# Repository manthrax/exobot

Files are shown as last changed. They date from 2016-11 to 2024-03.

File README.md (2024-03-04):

https://manthrax.github.io/exobot/index.html



BOM:

DROK DC Buck Converter x2
https://www.amazon.com/DROK-Numerical-Switching-Adjustable-Stabilizers/dp/B00BYTEHQO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

8*2 = 16$

Adafruit 16-Channel PWM / Servo HAT for Raspberry Pi - Mini Kit

https://www.amazon.com/Adafruit-16-Channel-PWM-Servo-Raspberry/dp/B00SI1SPHS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

20$ bucks.

Raspberry Pi 3 Model B Motherboard
https://www.amazon.com/Raspberry-Pi-RASP-PI-3-Model-Motherboard/dp/B01CD5VC92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
37$

TowerPro SG90 9G Micro Servo 10pk For RC Airplane Boat Helicopter Robot Controls
https://www.amazon.com/TowerPro-Micro-Airplane-Helicopter-Controls/dp/B01D6FEI1W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

22$

16+20+37+22 = 95$

sudo apt-get update
sudo apt-get install node
sudo npm install http
sudo npm install express
sudo npm install ws
sudo npm install adafruit-pca9685

sudo nano /etc/rc.local

Add this before the "exit 0" line.. this makes the bot code launch at startup.

su pi -c '~/bot/exobot/nodebot.sh < /dev/null &'

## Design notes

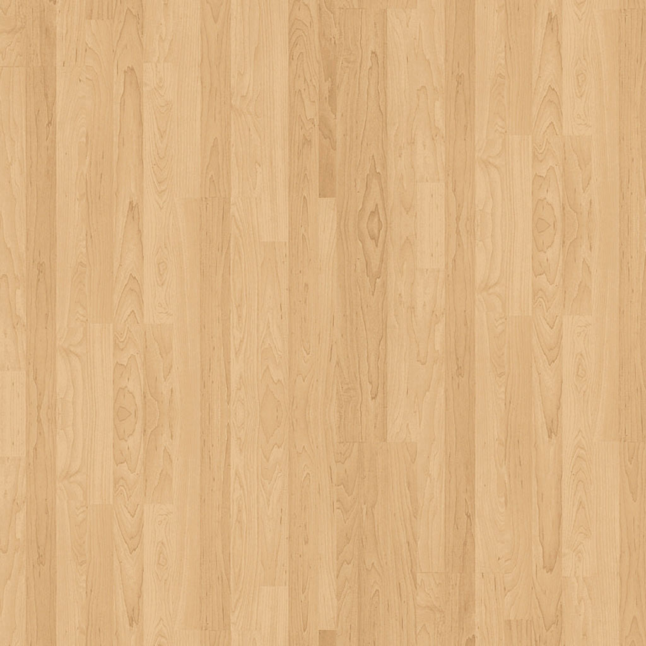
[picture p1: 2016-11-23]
woodfloor.jpg

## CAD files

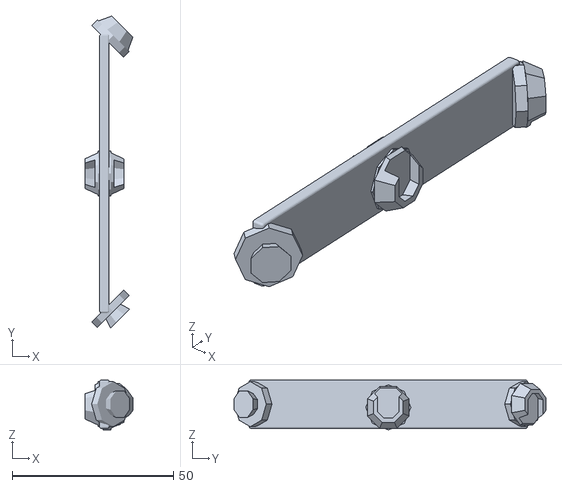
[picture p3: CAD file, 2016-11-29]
design/quadStrut.stl
14.8 x 96.7 x 15.5

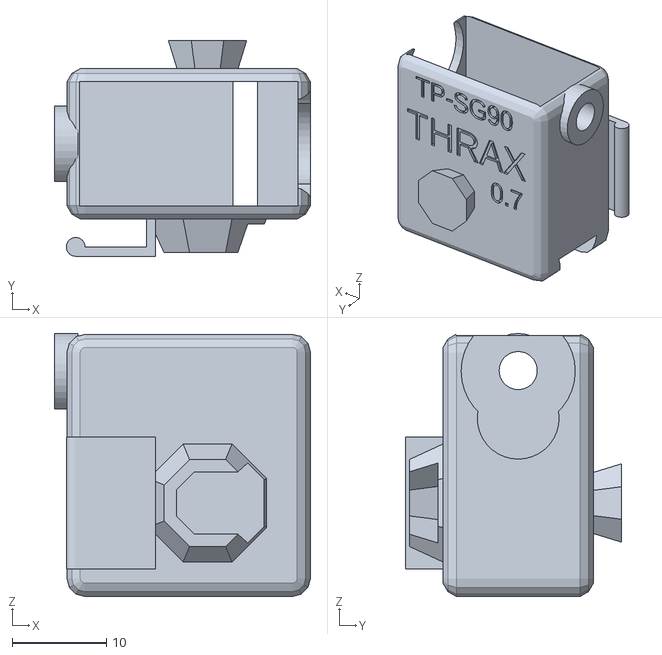
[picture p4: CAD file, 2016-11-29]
design/servoSleeveWithConnectors.stl
27.2 x 22.9 x 27.9

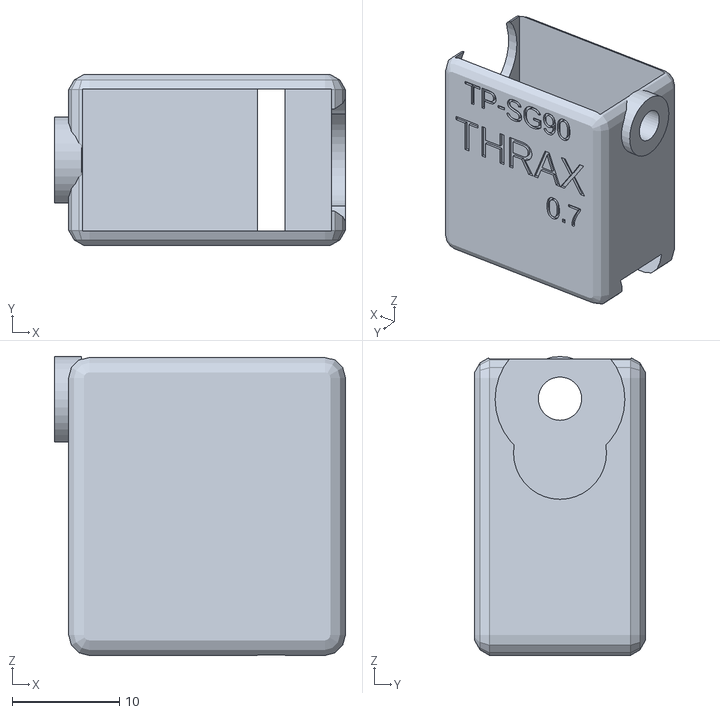
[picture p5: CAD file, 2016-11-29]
design/servoSleeve.stl
27.2 x 16.0 x 27.9

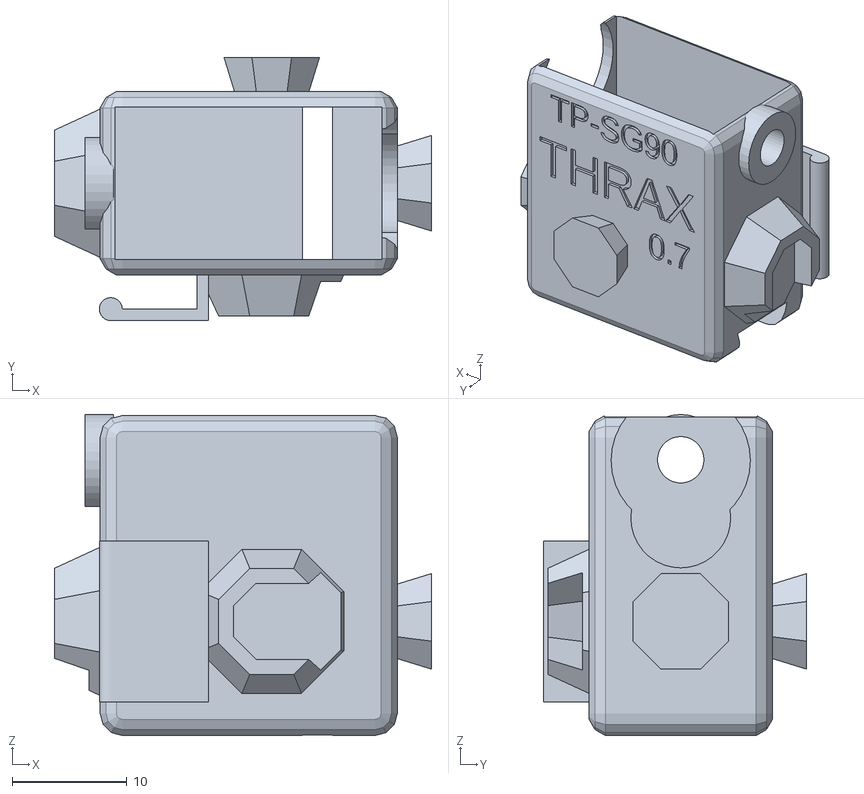
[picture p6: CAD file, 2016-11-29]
design/servoSleeveWithMultiConnectors.stl
32.8 x 22.9 x 27.9

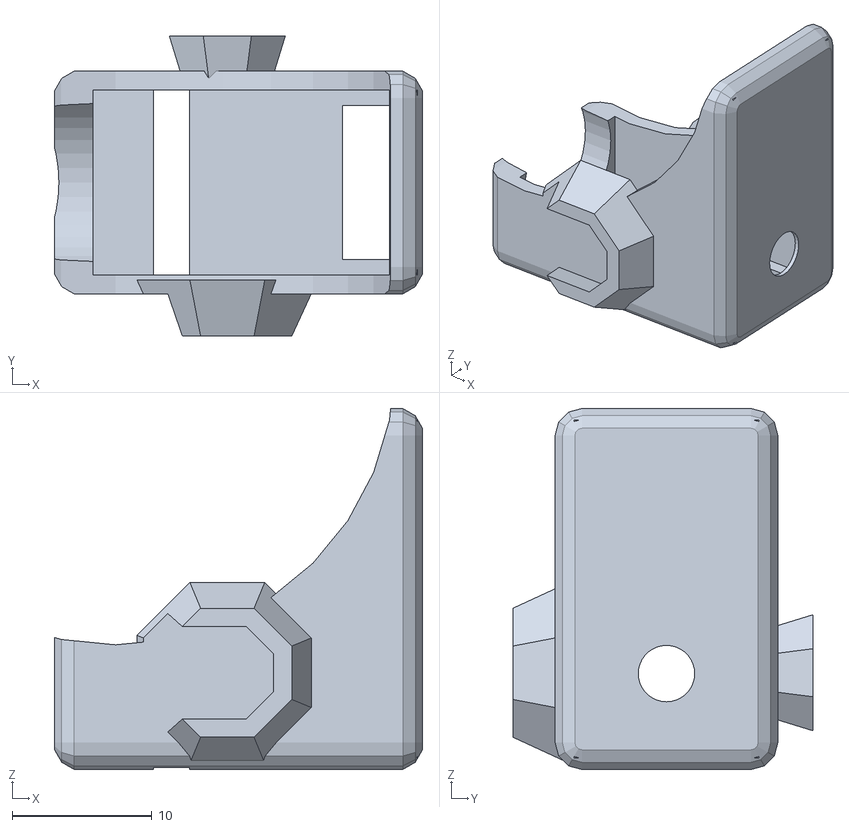
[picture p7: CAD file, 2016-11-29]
design/servoCage.stl
26.4 x 21.5 x 25.9

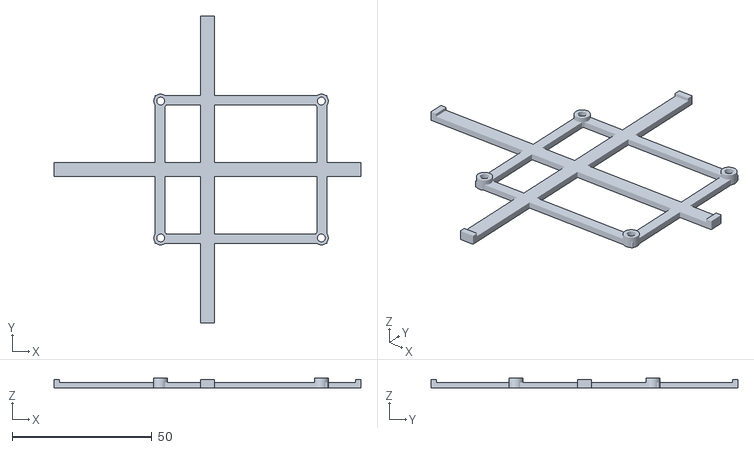
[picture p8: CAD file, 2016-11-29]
design/rackPi.stl
109.9 x 109.9 x 3.55

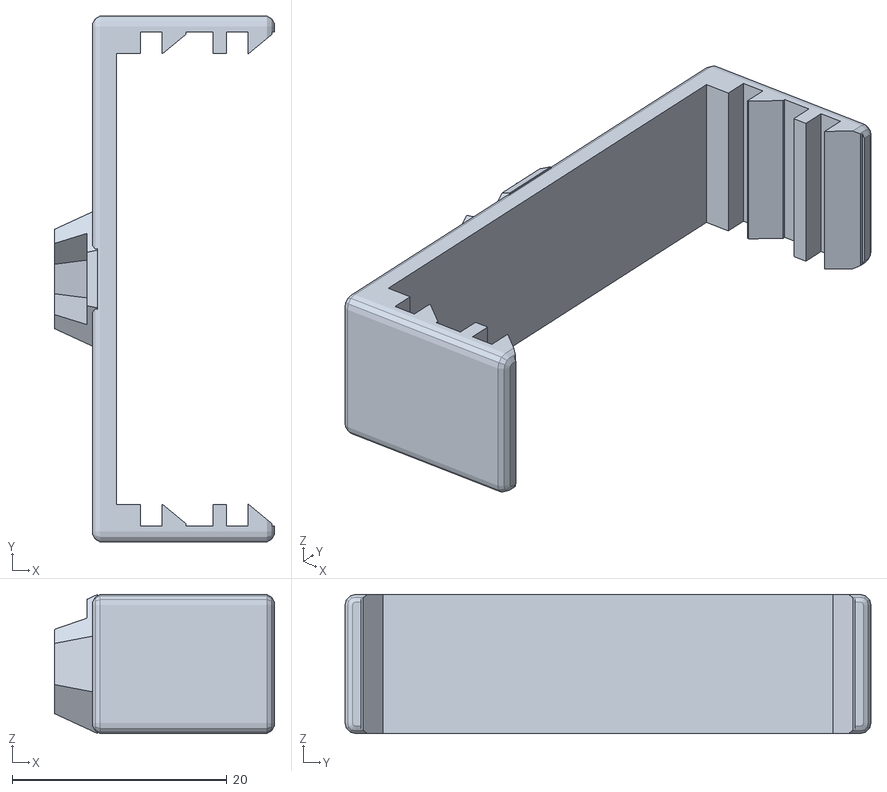
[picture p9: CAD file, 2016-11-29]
design/sensorClamp.stl
20.5 x 48.9 x 12.9

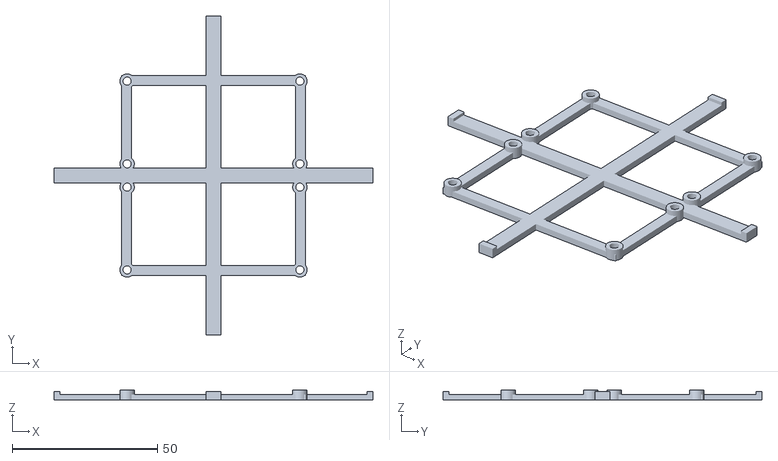
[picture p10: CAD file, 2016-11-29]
design/rackBuck.stl
109.9 x 109.9 x 3.55

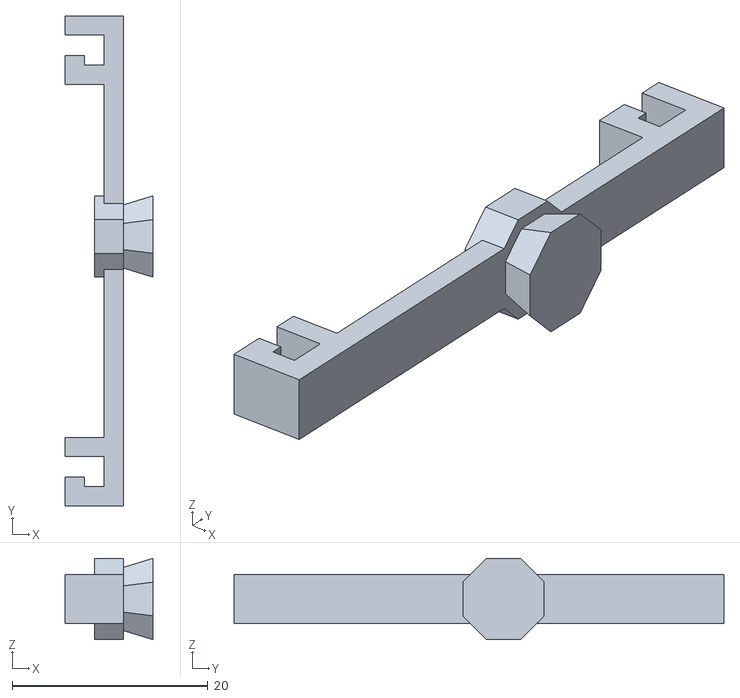
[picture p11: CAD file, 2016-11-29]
design/rackShelfClip.stl
9.00 x 50.0 x 8.31

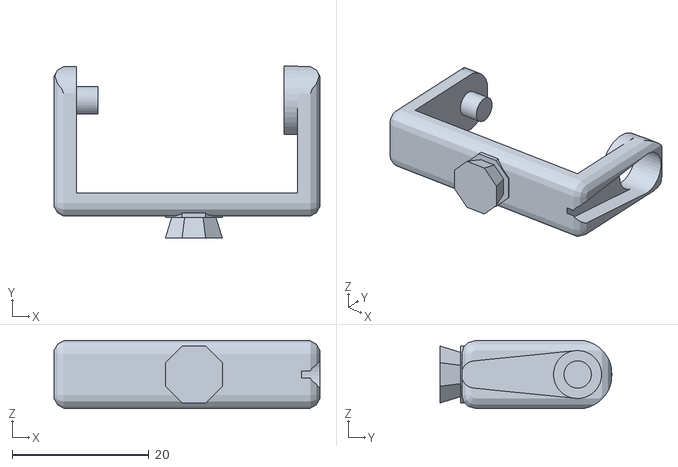
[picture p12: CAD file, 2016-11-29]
design/servoArm.stl
38.9 x 25.1 x 10.00

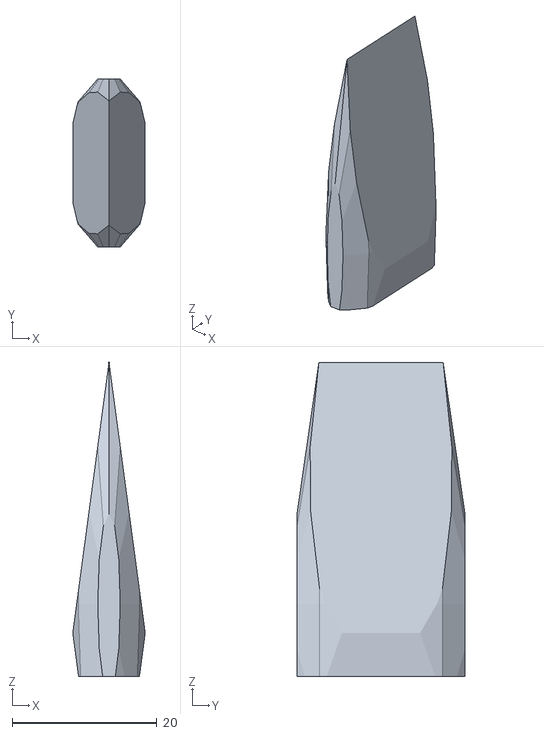
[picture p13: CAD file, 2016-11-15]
design/foot.stl
10.0 x 23.2 x 43.3

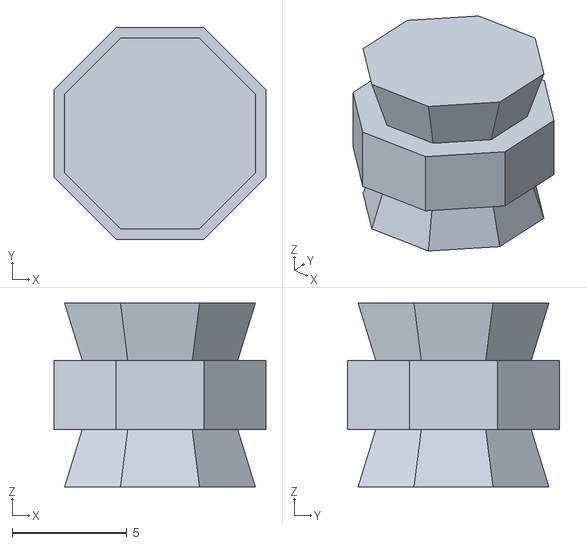
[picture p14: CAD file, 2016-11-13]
design/m2m.stl
9.24 x 9.24 x 8.00

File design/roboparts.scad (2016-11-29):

// CSG-modules.scad - Basic usage of modules, if, color, $fs/$fa

// Change this to false to remove the helper geometry
debug = true;

// Global resolution
$fa = 5;    // Don't generate larger angles than 5 degrees
$fs = 0.2;  // Don't generate smaller facets than 0.1 mm
$fa = 10;    // Don't generate larger angles than 5 degrees

scaleFudge = 1.01;
roundCubes = true;

versionNo = "0.7";

//servoTabLength = 5;

wallThickness = 3;
//Radioshack 2730765
servoName = "RShack";
servoTabLength = 6;
servoBodyWidth = 12;
servoBodyHeight = 21;
servoTabThickness = 2.1;


//TowerPro SG-90
servoName = "TP-SG90";
servoTabLength = 8;//how far the tab sticks out
servoBodyWidth = 13.1;
servoBodyHeight = 23;
servoTabThickness = 2.58;



// Main geometry

//Render the part
partsOnly = true ;
legInset = 32;
nside = 4;  //Number of legs 6 = hexapod
segAngle = 360/nside;

baseRadius = 75;//54;

hardwareZOffset = -1;

piVerticalOffset = 8.5;
battVerticalOffset = -18;
buckVerticalOffset = 36.5;


br = baseRadius;
sa = segAngle;

//pp1 = [sin(0)*br,cos(0)*br,0];
//pp2 = [sin(sa)*br,cos(sa)*br,0];


function rvec(x,y,a) = [(sin(a)*x)+(cos(a)*y),(-cos(a)*x)+(sin(a)*y),0]; 

bo =   14;
pp1 = rvec(br,bo,0);
pp2 = rvec(br,-bo,sa);

chordRadius = norm((pp1+pp2)*0.5);
chordLength =  norm(pp2-pp1);



color0 = "Teal";//"LightGreen";
color1 = "LightBlue";
color2 = "Red";
color3 = "Orange";

rackBeamWidth = 23;


npart = 80;//17;//80;//70;//17;//15;
doPart(npart);

module doPart(part){

    if(part==0){ color(color0) translate([6,0,5]) rotate([90,0,90])  servoArm(); }
    
    if(part==5){ color(color0) translate([6,0,5]) rotate([0,0,0])  m2m(); }
    
    if(part==10){ color(color1) rotate([0,90,0]) calfSleeve(); }
    if(part==15){ color(color3) rotate([0,90,0]) calfSleeveWithConnectors(); }
    if(part==17){ color(color3) rotate([0,90,0]) calfMultiConnectorSleeve();}
    if(part==20){ translate([0,0,-50]) rotate([0,90,90]) foot(); }
    if(part==30){ color(color2) bodyClamp(); }
    if(part==40){ rotate([0,0,0]) bodyFrame(); }

    if(part==50){ color(color3) translate([0,0,9.5]) rotate([0,-90,0]) sensorMount(); }
    if(part==60){ color(color0) translate([6,0,12.5]) rotate([0,-90,0]) servoCage(); }

    if(part==65){ rotate([0,0,segAngle/2]) strut(); }
    
    if(part==70){ leg(); }
    if(part==80){ bot(); }//bodyClamp();}
    if(part == 90){
        servoCage();
        servoArm();
        #servo();
        #servoHorn();
    //   translate([0,0,14.5]) cube([6,6,6]);
    //barProxy();
        translate([-32,0,-1]) rotate([0,90,0])  sensorMount();
    }
    
    if(part == 100){
        rotate([90,0,0])rackShelfClip();
    }
    if(part == 110){
        rackRaspi();
    }
    if(part == 120){
        rackBuck();
    }
    
    if(part == 125){
        rotate([90,0,0]){
          servoBoardSpacer();
          translate([0,0,11.7]) boardHolePin();
        }
    }
    if(part == 130){
        rackVis();
    }
}



///

//Battery: 100x30x20
//RASPI: 87x57x37
//Buck converter 66x36x13


module servoBoardSpacer(){
    cylinder(10.5,2.5,2.5,center = true);
    cylinder(20.5,1.25,1.25,center = true);
}

module boardHolePin(){
    cylinder(2.5,2.5,2.5,center = true);
    translate([0,0,3])cylinder(6,1.25,1.25,center = true);
}


module hcube(dim,center = false){
    difference(){
        cube(dim,center);
        cube([dim.x-4,dim.y-4,dim.z+2],center);
    }
}

module hardware(){
    module buckConverter(){
        #hcube([66,36,13],center = true);
        translate([0,0,-5.0])color("Red") cube([59.5,28.5,2],center = true);
    }
    
        translate([0,0,battVerticalOffset]) #hcube([100,30,20],center = true);//battery
        
        translate([0,0,piVerticalOffset]) #hcube([87,57,25],center = true);//pi
        translate([12,0,piVerticalOffset-11.5]) color("Red") cube([57.5,49,2],center = true);//pi57.5,49

        translate([0, 18.5,buckVerticalOffset+9])  buckConverter();
        translate([0,-18.5,buckVerticalOffset+9])  buckConverter();
    
}

module rackShelfArm(){
    r1 = chordRadius/2;
    translate([r1-5,0,0])cube([chordRadius-6,5,2],center=true);
    translate([chordRadius-9,0,1.5])cube([2,5,1],center=true);//Tongue
}

module rackShelfArms(){
    for(i=[0:1:nside])
    rotate([0,0,segAngle*i]){
        rackShelfArm();
    }    
}


module socket(slot = false){
    if(slot){
        connectorSlot();
    }else{
        rotate([180,0,0])connectorWithBase();
    }
}

module rackShelfClip(){
    r2 = chordRadius-7;
    r1 = chordRadius-4;
//    translate([0,0,-r1]) rotate([180,0,0]) connectorSlot();
    maskWid = 6;
    slotWid = maskWid-1;
    module slotMask(){
       for(i=[-1:1:0]){
            translate([0,0,(43*i)+22.5]){
                cube([20,maskWid ,2.1],center = true);
                translate([9,0,1.5])cube([2,maskWid,1],center=true);//Tongue
            }
       }
    }
    
    translate([r1,0,0]){
        translate([-1,0,0])rotate([0,90,0]) socket(false);
        translate([0,0,-hardwareZOffset]){
            difference(){
                translate([-5,0,1.5]) cube([6,slotWid,50],center=true);
                translate([-14,0,0]) slotMask();
                translate([-8,0,1.5]) cube([8,maskWid,36],center=true);
            }
           // translate([-14,0,0]) slotMask();
        }
    }
}

module rackPinBase(dx,dy){
    dx2 = dx/2;
    dy2 = dy/2;
        module rackPin(){
            //translate([0,0,-3.5]) cylinder(4,1.4,1.4,center = true);
            translate([0,0,-0.8]) cylinder(3.5,2.5,2.5,center = true);
        }
    rotate([0,90,0]){
        translate([0,dx2,dy2])rotate([0,90,0])rackPin();
        translate([0,-dx2,dy2])rotate([0,90,0])rackPin();
        translate([0,dx2,-dy2])rotate([0,90,0])rackPin();
        translate([0,-dx2,-dy2])rotate([0,90,0])rackPin();
    }
}

module rackPins(dx,dy){
    dx2 = dx/2;
    dy2 = dy/2;
        module rackPin(){
            translate([0,0,-1.5]) cylinder(8,1.4,1.4,center = true);
        }
    rotate([0,90,0]){
        translate([0,dx2,dy2])rotate([0,90,0])rackPin();
        translate([0,-dx2,dy2])rotate([0,90,0])rackPin();
        translate([0,dx2,-dy2])rotate([0,90,0])rackPin();
        translate([0,-dx2,-dy2])rotate([0,90,0])rackPin();
    }
}

module rackPlate(dx,dy){
    dx2 = dx/2;
    dy2 = dy/2;
    rotate([0,90,0])//difference()
    {
        difference()
        {
            cube([2,dx+4,dy+4],center = true);
            cube([4,dx-3,dy-3],center = true);
        }
    }
    rackPinBase(dx,dy);
}



module rackRaspi(){//57.5 49
    translate([0,0,piVerticalOffset-15]){
        rackShelfArms();
        translate([12,0,0]){
            difference(){
                rackPlate(49,57.5);
                rackPins(49,57.5);
            }
        }
    }
}


module rackBuck(){
    spacing = 8;
    
    translate([0,0,buckVerticalOffset]){
        difference(){
            translate([0,0,0]){
                rackPlate(28.5*2+spacing,59.5);//28.5 59.5   35, 66
                rackPinBase(spacing,59.5);
            }
            rackPins(28.5*2+spacing,59.5);
            rackPins(spacing,59.5);
        }
        
        rackShelfArms();
    }
}

module allRacks(){
    rackBuck();
    rackRaspi();
}


module rackVis(){
    
    rotate([0,0,segAngle/2]){
        translate([0,0,-(hardwareZOffset+14)]){
            allRacks();
             hardware();
        }
        for(i=[0:1:nside])
        rotate([0,0,segAngle*i])
            rackShelfClip();
    }
}


module bodyClamp(){
    difference()
    {
        color("Purple") translate([0,0,-4]) cylinder(7,33,33,$fn=6,center = true);
      //  basePunch();
        bot();
        bodyFrame();
    }
}

module basePunch(scl=1){
    module punch(){
        scale(1.0){
        translate([0,-50,0]) rotate([0,0,30]) cylinder(28,16*scl,16*scl,$fn=nside,center = true);
        rotate([0,0,30]) translate([24.5,14,0]) cylinder(18,13.5*scl,13.5*scl,$fn=nside,center = true);
        }
    }
    rotate([0,0,90]) punch();
    rotate([0,0,30]) punch();
    rotate([0,0,150]) punch();
    rotate([0,0,-90]) punch();
    rotate([0,0,-30]) punch();
    rotate([0,0,-150]) punch();
    rotate([0,0,0]) cylinder(28,15,15,$fn=nside,center = true);
}

module bodyFrame(){
    //difference()
    {
        /*
        color("Blue") translate([0,0,-2.5]){
            cylinder(5,48,48,$fn=6,center = true);
            translate([0,0,6]) cylinder(15,38,48,$fn=nside,center = true);
        }
        basePunch();
        */
        botLegs();
    }
}

module botLegs(){
    thet = 360/nside;
    for(i=[0:1:nside-1]){
        rotate([0,0,thet*i]) leg();
    }
}

module bot(){
    rackVis();

    bodyFrame();
    botLegs();
}
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

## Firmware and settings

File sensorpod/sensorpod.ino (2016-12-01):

/*
  
  Emic 2 Text-to-Speech Module: Basic Demonstration       
                                                         
  Author: Joe Grand [www.grandideastudio.com]             
  Contact: support@parallax.com                            
  
  Program Description:
  
  This program provides a simple demonstration of the Emic 2 Text-to-Speech
  Module. Please refer to the product manual for full details of system 
  functionality and capabilities.

  Revisions:
  
  1.0 (February 13, 2012): Initial release
  
*/

// include the SoftwareSerial library so we can use it to talk to the Emic 2 module
#include <SoftwareSerial.h>
#include <Wire.h>

#define rxPin 8    // Serial input (connects to Emic 2 SOUT)
#define txPin 9    // Serial output (connects to Emic 2 SIN)
#define ledPin 13  // Most Arduino boards have an on-board LED on this pin

const int sigSonar = 2;
long lastPing = 0;

long duration;
int lastCM = 0;

int debugLevel = 0;
const byte i2cSlaveId = 8;

// set up a new serial port
SoftwareSerial emicSerial =  SoftwareSerial(rxPin, txPin);

void speak(const char* str){  
  emicSerial.print('S');
  emicSerial.print(str);
  emicSerial.print('\n');
  while (emicSerial.read() != ':'); // Wait here until the Emic 2 responds with a ":" indicating it's ready to accept the next command
}

volatile int gotData = 0;
volatile int gotCount = 0;
volatile int gotRequest = 0;
volatile int curCommand = 0;
void requestCallback(){
  if(curCommand==0){
    for(int i=0;i<4;i++)Wire.write(((char*)&duration)[i]);
  }
  gotRequest=1;
}

char byteBuf[256];

void receiveCallback(int count){
  int i=0;
  gotCount = count;
  while (Wire.available()>0){byteBuf[i]= (char)Wire.read();i=(i+1)&255;} // receive byte as a character
  byteBuf[i]=0;
  gotData = i;
}

void setup()  // Set up code called once on start-up
{

  Wire.begin(i2cSlaveId);
  
  Wire.onReceive(receiveCallback);
  Wire.onRequest(requestCallback);
  
  // define pin modes
  pinMode(ledPin, OUTPUT);
  pinMode(rxPin, INPUT);
  pinMode(txPin, OUTPUT);
  
  // set the data rate for the SoftwareSerial port
  emicSerial.begin(9600);

  digitalWrite(ledPin, LOW);  // turn LED off
  
  /*
    When the Emic 2 powers on, it takes about 3 seconds for it to successfully
    intialize. It then sends a ":" character to indicate it's ready to accept
    commands. If the Emic 2 is already initialized, a CR will also cause it
    to send a ":"
  */
  emicSerial.print('\n');             // Send a CR in case the system is already up
  while (emicSerial.read() != ':');   // When the Emic 2 has initialized and is ready, it will send a single ':' character, so wait here until we receive it
  delay(10);                          // Short delay
  emicSerial.flush();                 // Flush the receive buffer
}


void loop()  // Main code, to run repeatedly
{
  // Speak some text
  digitalWrite(ledPin, HIGH);         // Turn on LED while Emic is outputting audio
  speak("My name is legion. For we are many.");
  digitalWrite(ledPin, LOW);
 
  delay(500);    // 1/2 second delay
    
  // Sing a song
  emicSerial.print("D2\n");
  digitalWrite(ledPin, HIGH);         // Turn on LED while Emic is outputting audio
  while (emicSerial.read() != ':'){
    delay(100);   // Wait here until the Emic 2 responds with a ":" indicating it's ready to accept the next command
  }
  digitalWrite(ledPin, LOW);

  speak("System ready.");
  int   blinkToggle=0;
  while(1)      // Demonstration complete!
  {
    if(blinkToggle==0){
      
      digitalWrite(ledPin, HIGH);
    }else if(blinkToggle==128){
      digitalWrite(ledPin, LOW);
    }
    blinkToggle=(blinkToggle+1)&255;

    if(gotData>0){
        int cmd = byteBuf[0];
        curCommand = cmd;
        if(cmd==123){
          String str = (const char*)(&byteBuf[1]);
          speak(str.c_str());
        }else if(cmd==0){
          pingSonar();
        }else if(cmd==126){
          debugLevel = 1;
          speak("debug 1");
        }else if(cmd==127){
          debugLevel = 0;
          speak("debug 0");
        }
        
        if(debugLevel){
          String str;
          str = "Got receive : ";
          str += gotData;
          speak(str.c_str());
  
          str = "Data count is: ";
          str += gotCount;
          speak(str.c_str());
          
          str = "First byte is: ";
          str += (int)(byteBuf[0]);
          speak(str.c_str());
        }
        gotData = 0;
    }

    if(gotRequest>0){
      if(debugLevel){
        speak("Got Request.");
      }
      gotRequest = 0;
    }
    delay(1);
  }
}

void pingSonar() {
    
  long inches, cm;
  
  pinMode(sigSonar, OUTPUT);  
  digitalWrite(sigSonar, LOW);
  delay(2);
  digitalWrite(sigSonar, HIGH);
  delay(10);
  digitalWrite(sigSonar, LOW);
  
  pinMode(sigSonar, INPUT);
  duration = pulseIn(sigSonar, HIGH);
  
  inches = microsecondsToInches(duration);
  cm = microsecondsToCentemeters(duration);
  /*
  emicSerial.print("Sinches ");
  emicSerial.print(inches);
  emicSerial.print(" cm, ");
  emicSerial.print(cm);
  emicSerial.print(" centemeters");
  emicSerial.print("\n");
  */
  if(lastCM!=cm){
    lastCM = cm;
      if(debugLevel){
        emicSerial.print("S ");
        emicSerial.print(cm);
        emicSerial.print("\n");
        while (emicSerial.read() != ':');   // Wait here until the Emic 2 responds with a ":" indicating it's ready to accept the next command
      }
  }
  //delay(500);
}
  
  long microsecondsToInches(long microseconds) {
    
    return microseconds / 74 /2;
  }
  
  long microsecondsToCentemeters(long microseconds) {
    
    return microseconds / 29 / 2;
  }

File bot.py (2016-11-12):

from __future__ import division
import time
import Adafruit_PCA9685
import curses
import json

# Uncomment to enable debug output.
#import logging
#logging.basicConfig(level=logging.DEBUG)
# Initialise the PCA9685 using the default address (0x40).
pwm = Adafruit_PCA9685.PCA9685()

# Alternatively specify a different address and/or bus:
#pwm = Adafruit_PCA9685.PCA9685(address=0x41, busnum=2)


state = []

try:
    with open('botstate.json') as json_data:
        state = json.load(json_data)
    print(state)

except Error:
    state = []


nservos = 8

# Configure min and max servo pulse lengths
servo_min = 150  # Min pulse length out of 4096
servo_max = 600  # Max pulse length out of 4096

servo_mid = int((servo_min+servo_max)/2)
servo_rng = servo_max-servo_min;

stdscr = curses.initscr()
curses.cbreak()
stdscr.keypad(1)

stdscr.addstr(0,10,"Hit 'q' to quit")
stdscr.refresh()


key = ''


# Helper function to make setting a servo pulse width simpler.
def set_servo_pulse(channel, pulse):
    pulse_length = 1000000    # 1,000,000 us per second
    pulse_length //= 60       # 60 Hz
    print('{0}us per period'.format(pulse_length))
    pulse_length //= 4096     # 12 bits of resolution
    print('{0}us per bit'.format(pulse_length))
    pulse *= 1000
    pulse //= pulse_length
    pwm.set_pwm(channel, 0, pulse)

sv = []
ss = 0;

def svset(idx,pos):
    global ss;
    ss = idx;
    sv[ss]=pos;
    svpwm = int(((sv[ss]*servo_rng)/2)+servo_mid)
    pwm.set_pwm(ss,0,svpwm)
    

def disableServo(idx):
    pwm.set_pwm(idx,0,0)

def disableServos():
    for x in range(0,nservos):
        disableServo(x);

def resetServos():
    # Set frequency to 60hz, good for servos.
    pwm.set_pwm_freq(60)
    for x in range(0,nservos):
    
        stdscr.addstr(15,0,'Moving servo on channel '+str(x)+'         ')
        stdscr.refresh()
        pwm.set_pwm(x,0,servo_mid)
        time.sleep(0.25)
        disableServo(x)
        sv.append(0.0)
    #while True:
        # Move servo on channel O between extremes.
        #set_servo_pulse(0, servo_mid)
        #k = raw_input("?")
        #print(k)
        #time.sleep(1)
        #set_servo_pulse(1, servo_mid)



def svo(off):
    sv[ss]+=off
    if(sv[ss]<-1.0): sv[ss]=-1.0
    elif (sv[ss]>1.0): sv[ss]=1.0
    svpwm = int(((sv[ss]*servo_rng)/2)+servo_mid)
    pwm.set_pwm(ss,0,svpwm)
    stdscr.addstr(6,5,str(sv[ss])+"   "+str(svpwm)+"       ");
        

def svi(off):
    global ss
    ss += off
    if(ss<0): ss=0
    elif (ss>=len(sv)): ss=len(sv)-1
    stdscr.addstr(1,5,str(ss)+"   ");



resetServos()

while key != ord('q'):
    key = stdscr.getch()
    #stdscr.addch(20,25,key)
    stdscr.refresh()
    if key == curses.KEY_UP:
        stdscr.addstr(2, 20, "Up")
        svo(0.1)
    elif key == curses.KEY_DOWN:
        stdscr.addstr(4, 20, "Down")
        svo(-0.1)
    elif key == curses.KEY_LEFT:
        stdscr.addstr(3, 15, "Left")
        svi(-1)
    elif key == curses.KEY_RIGHT:
        stdscr.addstr(3, 25, "Right")
        svi(1)
    elif key == ord('r'):
        resetServos();
    elif key == ord('k'):
        for x in range(0,8):
            svset(x,0.5)
            time.sleep(0.15)
        for x in range(0,8):
            svset(x,-0.5)
            time.sleep(0.15)
    elif key == ord('x'):
        disableServos();

curses.endwin()

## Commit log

2016-11-06 Delay between servo sets
2016-11-06 Add reset cmd R
    [bot.py]
2016-11-06 Fix servo stress test
    [bot.py]
